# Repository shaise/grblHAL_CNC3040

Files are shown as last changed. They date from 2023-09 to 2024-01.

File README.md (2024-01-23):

# grblHAL_CNC3040 [WIP]
Hardware implementation of the grblHAL driver to work with Chinese CNC3040 type of machines  

This project is intended to upgrade any cnc machine that is controlled via parallel port such as the popular chinese CNC3040.  
Instead of having a dedicated LinuxCNC PC or mach32, This device connects directly to the CNC's controller, and can be controlled using any grbl Sender sw via USB connection or even WiFi!  
This device supports an optional stand-alone KeyPad, that is also included in this project.  

This project is based on the great work of @terjeio and his [GrblHAL](https://github.com/grblHAL) project. Thanks!

## Some images:
Open driver  
Closed driver  
Keypad  

## Driver and KeyPad Assembly:
For instructions how to assemble, program and use the devices refer to the Wiki.

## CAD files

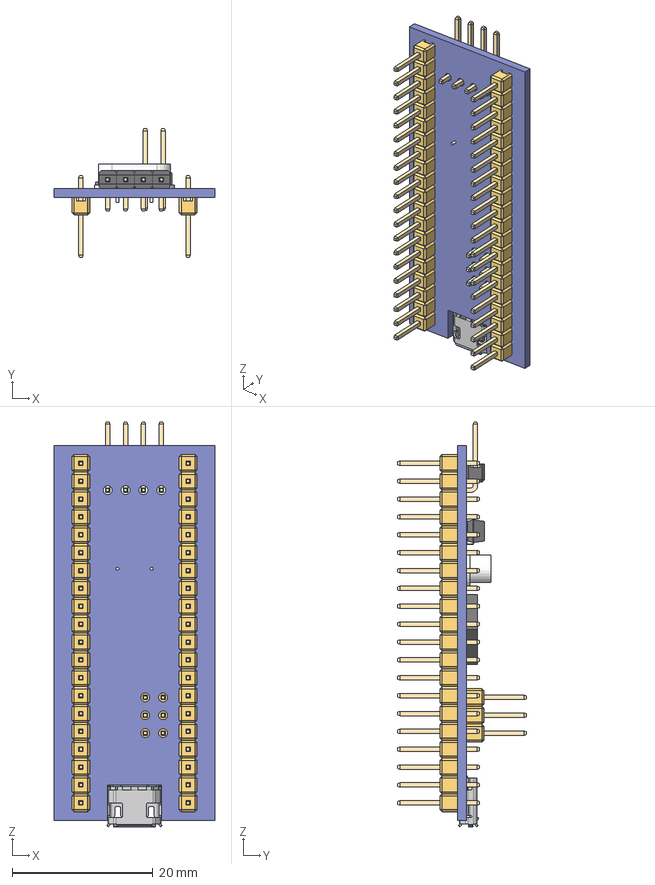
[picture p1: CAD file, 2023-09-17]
hardware/CNC3040_Keypad/models/STM32F103C8T6_Blue_Pill v6.step
22.9 x 18.3 x 57.6 mm
Oscillator_HC-49/S
STM32F103C8T6_BluePill_Board
Oscillator_MC-306
STM32_LQFP48
Tactile_SMD_5x5mm
Header_L4_10x4.8
Header_Male_2x3x11.6
Header_Male_1x20x11.6 x 2

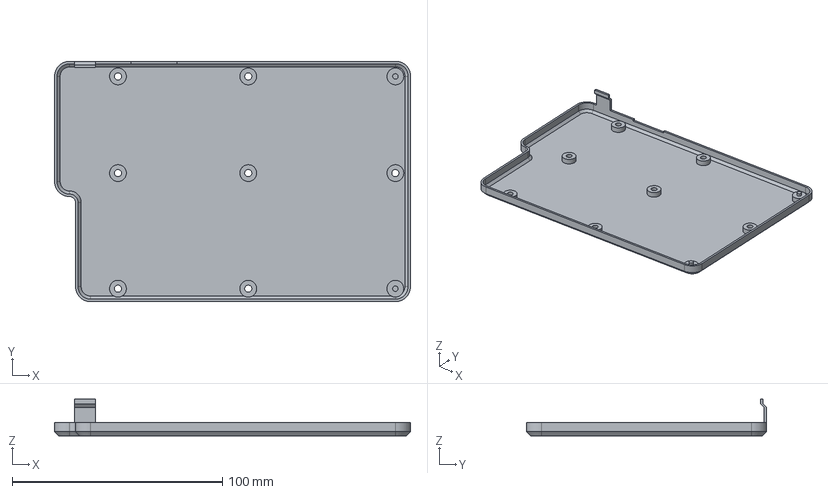
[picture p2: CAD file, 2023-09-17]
mechanics/KeyPadBox.FCStd
169.4 x 114.4 x 17.4 mm

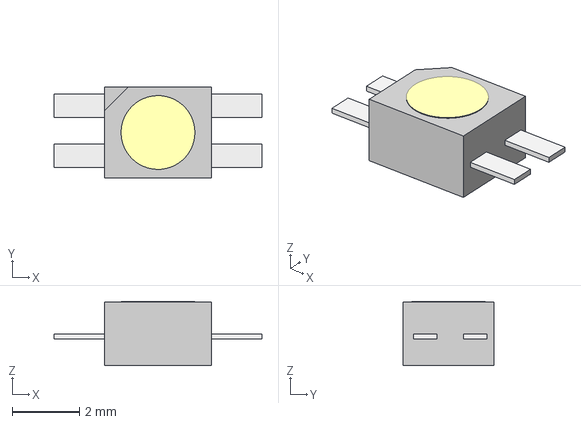
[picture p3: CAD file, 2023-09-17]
hardware/CNC3040_Keypad/models/LTST-A683CEGBW.step
6.20 x 2.70 x 1.92 mm

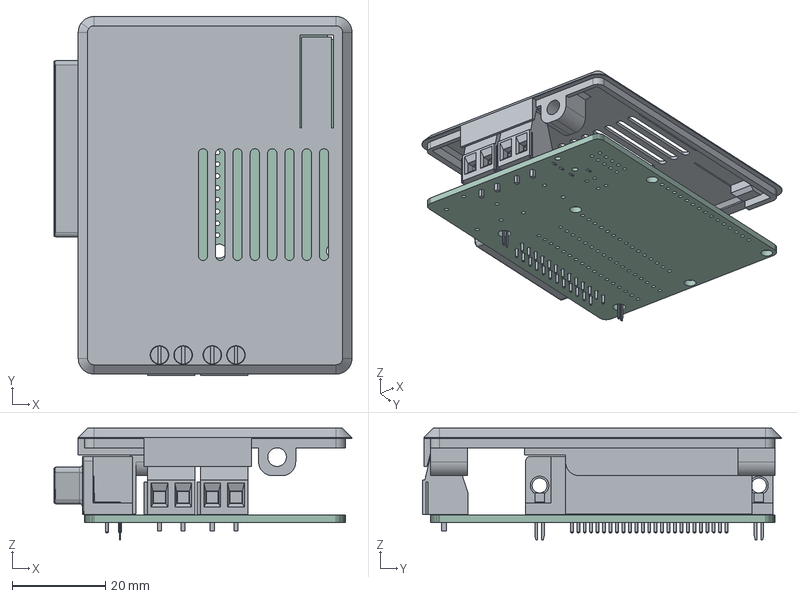
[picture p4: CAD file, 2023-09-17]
mechanics/CNC3040_Box.FCStd
64.0 x 77.1 x 24.0 mm
GrblHAL_CNC3040 PCB
Top

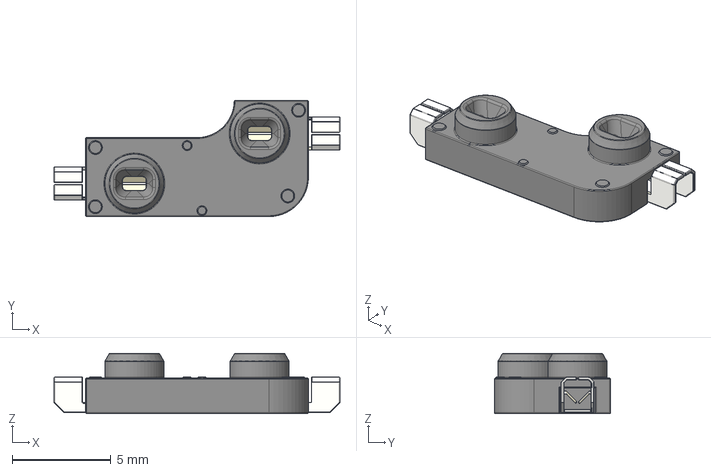
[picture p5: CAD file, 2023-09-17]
hardware/CNC3040_Keypad/models/KailhSocket.stp
14.5 x 5.89 x 3.05 mm

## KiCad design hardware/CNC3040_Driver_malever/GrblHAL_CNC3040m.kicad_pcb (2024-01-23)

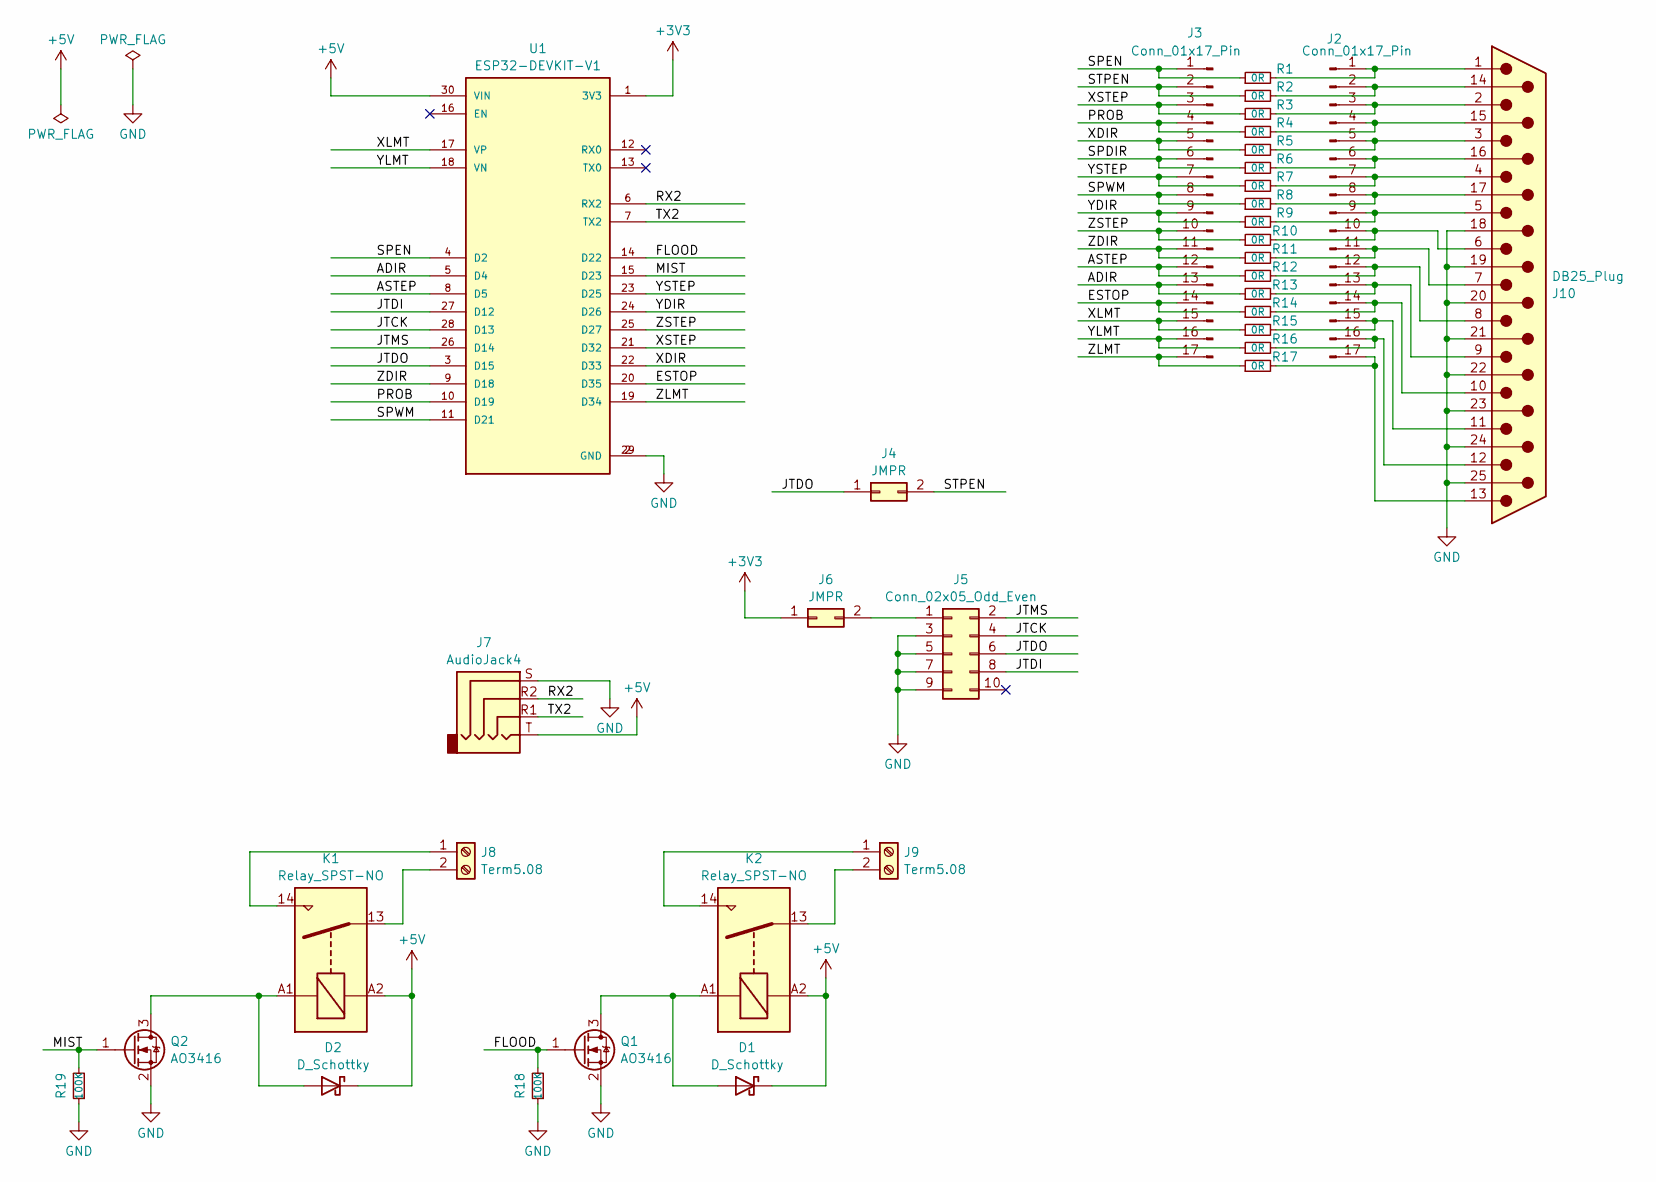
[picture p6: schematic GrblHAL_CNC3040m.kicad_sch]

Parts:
D1, D2: D_Schottky; D_SMA
J2, J3: Conn_01x17_Pin; PinHeader_1x17_P2.54mm_Vertical
J4, J6: JMPR; PinHeader_1x02_P2.54mm_Vertical
J5: Conn_02x05_Odd_Even; IDC-Header_2x05_P2.54mm_Vertical
J7: AudioJack4; Jack_3.5mm_PJ-320A
J8, J9: Term5.08; TerminalBlock_Phoenix_MKDS-1,5-2-5.08_1x02_P5.08mm_Horizont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
J10: DB25_Plug; DSUB-25_Male_Horizontal_P2.77x2.84mm_EdgePinOffset4.94mm_Ho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
K1, K2: Relay_SPST-NO; Relay_HF32FV-G
Q1, Q2: AO3416; SOT-23-3
R1, R2, R3, R4, R5, R6, R7, R8, R9, R10, R11, R12, R13, R14, R15, R16, R17: 0R; R_0603_1608Metric
R18, R19: 100K; R_0603_1608Metric
U1: ESP32-DEVKIT-V1; MODULE_ESP32_DEVKIT_V1; PARTREV N/A

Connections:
+3V3: J6.1, U1.1 (3V3)
+5V: D1.1 (K), D2.1 (K), J7.T, K1.A2, K2.A2, U1.30 (VIN)
/ADIR: J3.13, R13.1, U1.5 (D4)
/ASTEP: J3.12, R12.1, U1.8 (D5)
/ESTOP: J3.14, R14.1, U1.20 (D35)
/FLOOD: Q1.1 (G), R18.2, U1.14 (D22)
/JTCK: J5.4, U1.28 (D13)
/JTDI: J5.8, U1.27 (D12)
/JTDO: J4.1, J5.6, U1.3 (D15)
/JTMS: J5.2, U1.26 (D14)
/MIST: Q2.1 (G), R19.2, U1.15 (D23)
/PROB: J3.4, R4.1, U1.10 (D19)
/RX2: J7.R2, U1.6 (RX2)
/SPDIR: J3.6, R6.1
/SPEN: J3.1, R1.1, U1.4 (D2)
/SPWM: J3.8, R8.1, U1.11 (D21)
/STPEN: J3.2, J4.2, R2.1
/TX2: J7.R1, U1.7 (TX2)
/XDIR: J3.5, R5.1, U1.22 (D33)
/XLMT: J3.15, R15.1, U1.17 (VP)
/XSTEP: J3.3, R3.1, U1.21 (D32)
/YDIR: J3.9, R9.1, U1.24 (D26)
/YLMT: J3.16, R16.1, U1.18 (VN)
/YSTEP: J3.7, R7.1, U1.23 (D25)
/ZDIR: J3.11, R11.1, U1.9 (D18)
/ZLMT: J3.17, R17.1, U1.19 (D34)
/ZSTEP: J3.10, R10.1, U1.25 (D27)
GND: J5.3, J5.5, J5.7, J5.9, J7.S, J10.18, J10.19, J10.20, J10.21, J10.22, J10.23, J10.24, J10.25, Q1.2 (S), Q2.2 (S), R18.1, R19.1, U1.2 (GND), U1.29 (GND)
unnamed: D1.2 (A), K2.A1, Q1.3 (D)
unnamed: D2.2 (A), K1.A1, Q2.3 (D)
unnamed: J2.1, J10.1, R1.2
unnamed: J2.3, J10.2, R3.2
unnamed: J2.5, J10.3, R5.2
unnamed: J2.7, J10.4, R7.2
unnamed: J2.9, J10.5, R9.2
unnamed: J2.10, J10.6, R10.2
unnamed: J2.11, J10.7, R11.2
unnamed: J2.12, J10.8, R12.2
unnamed: J2.13, J10.9, R13.2
unnamed: J2.14, J10.10, R14.2
unnamed: J2.15, J10.11, R15.2
unnamed: J2.16, J10.12, R16.2
unnamed: J2.17, J10.13, R17.2
unnamed: J5.1, J6.2
unnamed: J8.1, K1.14
unnamed: J8.2, K1.13
unnamed: J9.1, K2.14
unnamed: J9.2, K2.13
unnamed: J2.2, J10.14, R2.2
unnamed: J2.4, J10.15, R4.2
unnamed: J2.6, J10.16, R6.2
unnamed: J2.8, J10.17, R8.2

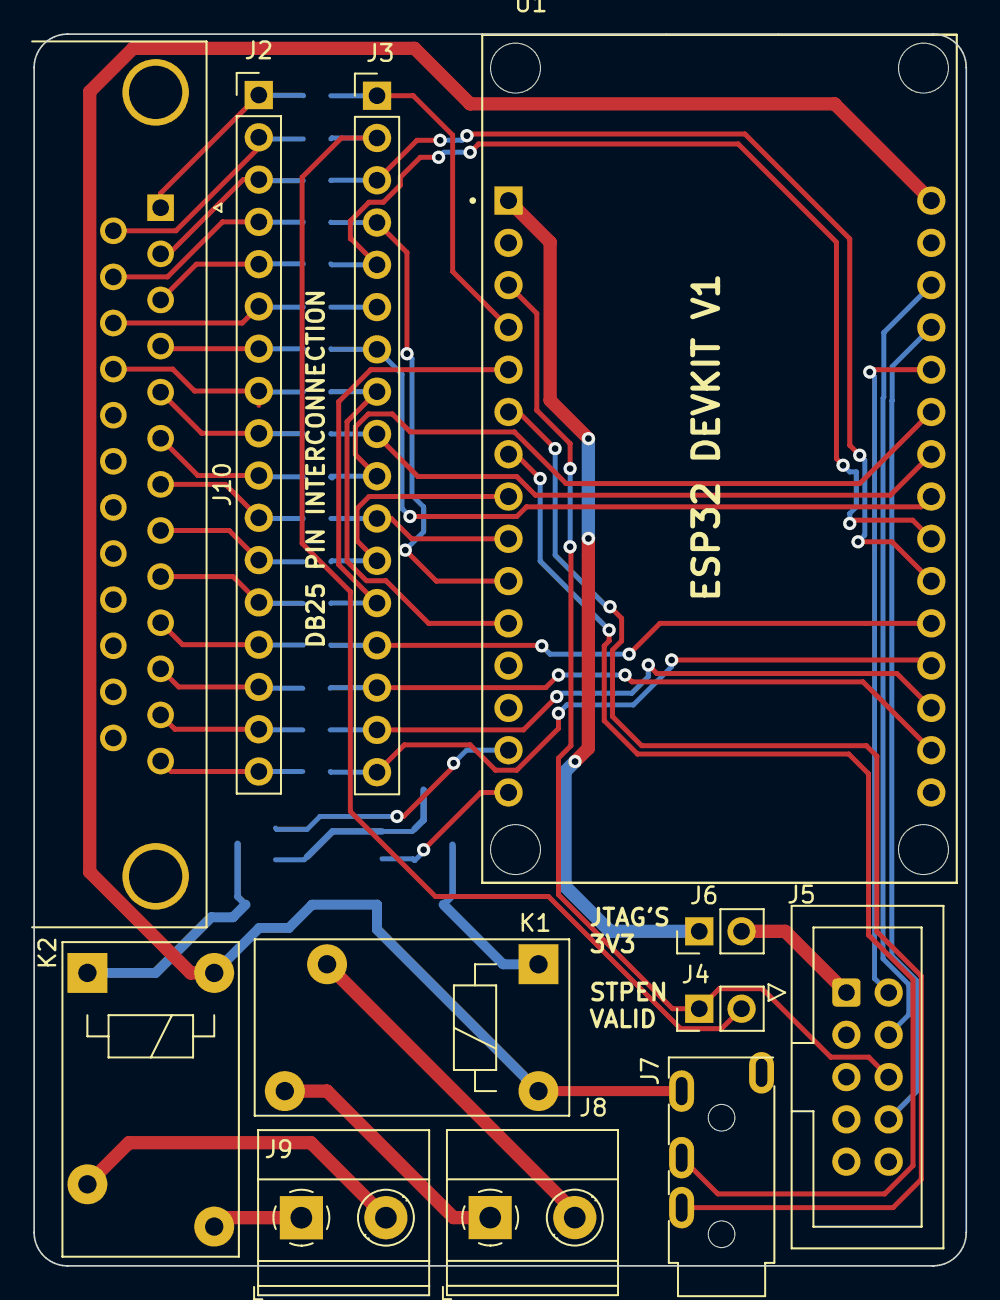
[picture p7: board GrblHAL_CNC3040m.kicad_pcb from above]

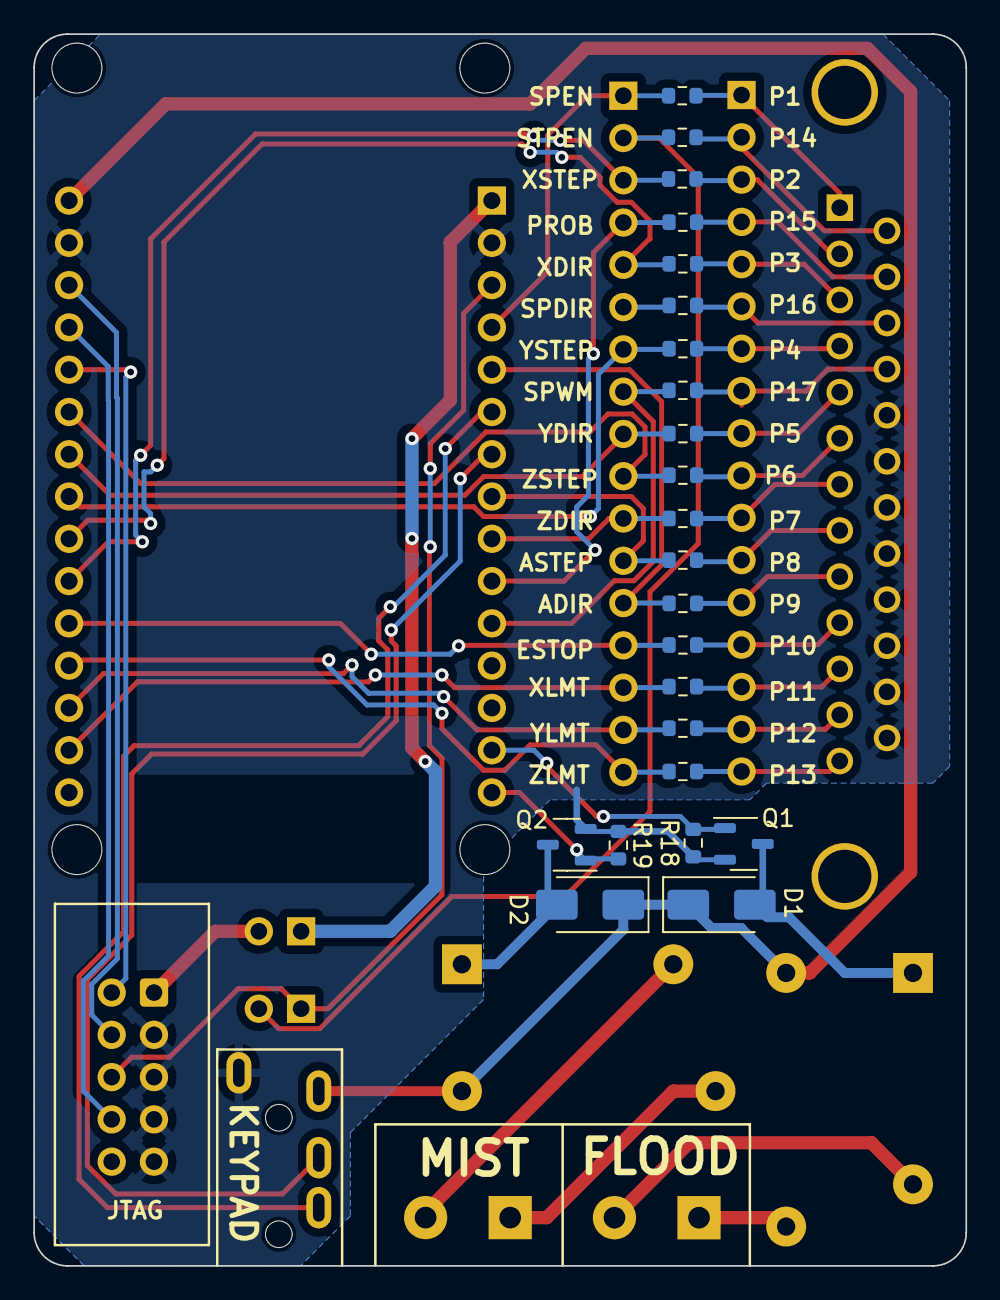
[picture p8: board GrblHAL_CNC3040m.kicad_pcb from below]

Board: 2 copper layers, 56.0 x 74.0 mm, 35 parts (23 on the bottom side), 52 nets.

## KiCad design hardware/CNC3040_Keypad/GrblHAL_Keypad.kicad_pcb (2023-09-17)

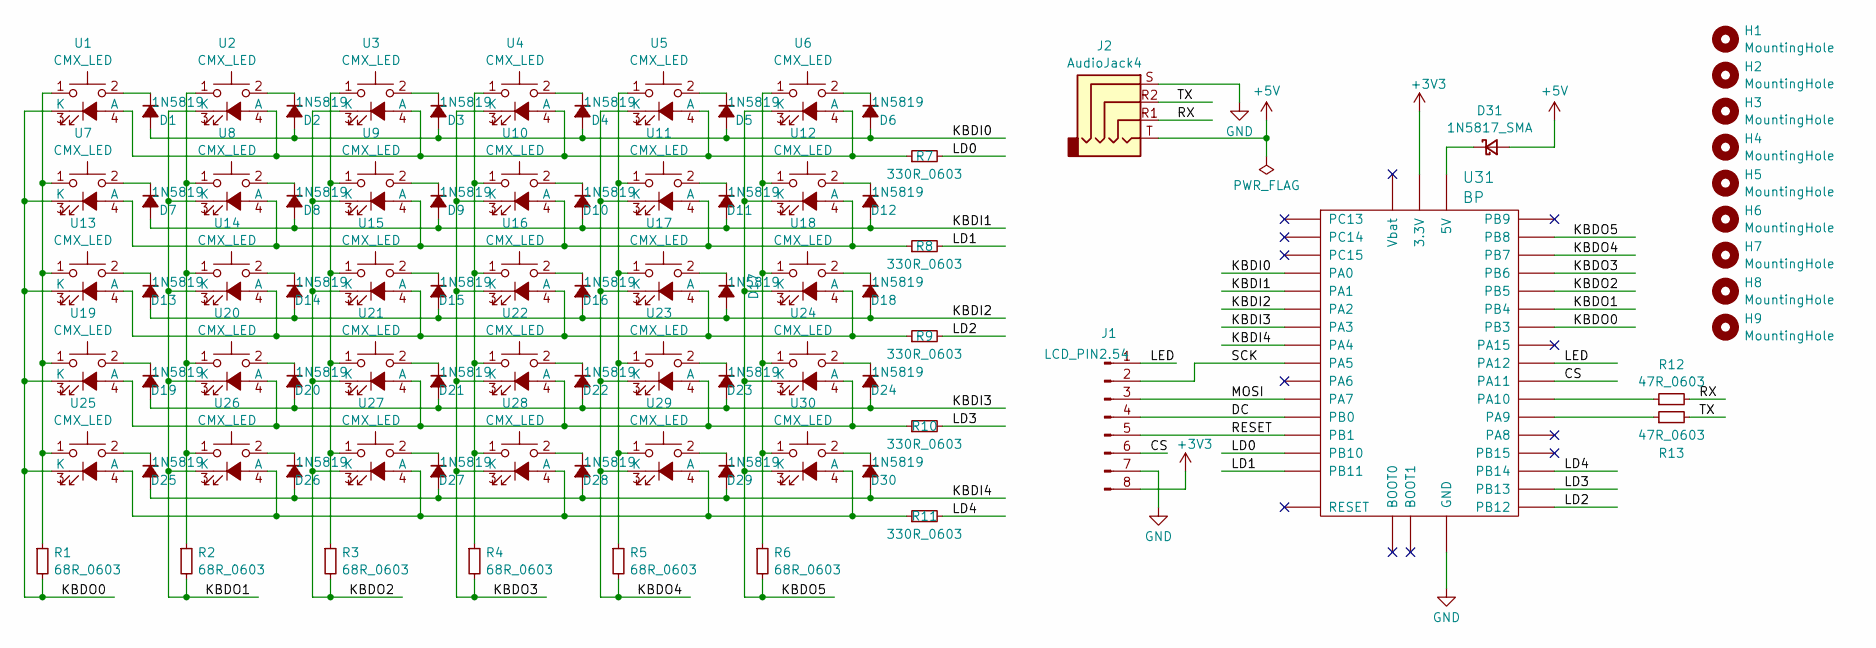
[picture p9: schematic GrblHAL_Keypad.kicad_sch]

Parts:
D1, D2, D3, D4, D5, D6, D7, D8, D9, D10, D11, D12, D13, D14, D15, D16, D17, D18, D19, D20, D21, D22, D23, D24, D25, D26, D27, D28, D29, D30: 1N5819; D_SOD-123
D31: 1N5817_SMA; D_SMA
H1, H2, H3, H4, H5, H6, H7, H8, H9: MountingHole; MountingHole_3.2mm_M3
J1: LCD_PIN2.54; PinHeader_1x08_P2.54mm_Vertical
J2: AudioJack4; Jack_3.5mm_PJ-320A
R1, R2, R3, R4, R5, R6: 68R_0603; R_0603_1608Metric
R7, R8, R9, R10, R11: 330R_0603; R_0603_1608Metric
R12, R13: 47R_0603; R_0603_1608Metric
U1, U2, U3, U4, U5, U6, U7, U8, U9, U10, U11, U12, U13, U14, U15, U16, U17, U18, U19, U20, U21, U22, U23, U24, U25, U26, U27, U28, U29, U30: CMX_LED; CherryMX_1.00u_KailhSocket_LED
U31: BP; BLUEPILL-BARE

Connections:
+3V3: J1.8, U31.3V3 (3.3V)
+5V: D31.2 (A), J2.T
/CS: J1.6, U31.PA11
/DC: J1.4, U31.PB0
/KBDI0: D1.2 (A), D2.2 (A), D3.2 (A), D4.2 (A), D5.2 (A), D6.2 (A), U31.PA0
/KBDI1: D7.2 (A), D8.2 (A), D9.2 (A), D10.2 (A), D11.2 (A), D12.2 (A), U31.PA1
/KBDI2: D13.2 (A), D14.2 (A), D15.2 (A), D16.2 (A), D17.2 (A), D18.2 (A), U31.PA2
/KBDI3: D19.2 (A), D20.2 (A), D21.2 (A), D22.2 (A), D23.2 (A), D24.2 (A), U31.PA3
/KBDI4: D25.2 (A), D26.2 (A), D27.2 (A), D28.2 (A), D29.2 (A), D30.2 (A), U31.PA4
/KBDO0: R1.2, U1.3 (K), U7.3 (K), U13.3 (K), U19.3 (K), U25.3 (K), U31.PB3
/KBDO1: R2.2, U2.3 (K), U8.3 (K), U14.3 (K), U20.3 (K), U26.3 (K), U31.PB4
/KBDO2: R3.2, U3.3 (K), U9.3 (K), U15.3 (K), U21.3 (K), U27.3 (K), U31.PB5
/KBDO3: R4.2, U4.3 (K), U10.3 (K), U16.3 (K), U22.3 (K), U28.3 (K), U31.PB6
/KBDO4: R5.2, U5.3 (K), U11.3 (K), U17.3 (K), U23.3 (K), U29.3 (K), U31.PB7
/KBDO5: R6.2, U6.3 (K), U12.3 (K), U18.3 (K), U24.3 (K), U30.3 (K), U31.PB8
/LD0: R7.2, U31.PB10
/LD1: R8.2, U31.PB11
/LD2: R9.2, U31.PB12
/LD3: R10.2, U31.PB13
/LD4: R11.2, U31.PB14
/LED: J1.1, U31.PA12
/MOSI: J1.3, U31.PA7
/RESET: J1.5, U31.PB1
/RX: J2.R1, R12.2
/SCK: J1.2, U31.PA5
/TX: J2.R2, R13.2
GND: J1.7, J2.S, U31.G (GND)
unnamed: D1.1 (K), U1.2
unnamed: D2.1 (K), U2.2
unnamed: D3.1 (K), U3.2
unnamed: D4.1 (K), U4.2
unnamed: D5.1 (K), U5.2
unnamed: D6.1 (K), U6.2
unnamed: D7.1 (K), U7.2
unnamed: D8.1 (K), U8.2
unnamed: D9.1 (K), U9.2
unnamed: D10.1 (K), U10.2
unnamed: D11.1 (K), U11.2
unnamed: D12.1 (K), U12.2
unnamed: D13.1 (K), U13.2
unnamed: D14.1 (K), U14.2
unnamed: D15.1 (K), U15.2
unnamed: D16.1 (K), U16.2
unnamed: D17.1 (K), U17.2
unnamed: D18.1 (K), U18.2
unnamed: D19.1 (K), U19.2
unnamed: D20.1 (K), U20.2
unnamed: D21.1 (K), U21.2
unnamed: D22.1 (K), U22.2
unnamed: D23.1 (K), U23.2
unnamed: D24.1 (K), U24.2
unnamed: D25.1 (K), U25.2
unnamed: D26.1 (K), U26.2
unnamed: D27.1 (K), U27.2
unnamed: D28.1 (K), U28.2
unnamed: D29.1 (K), U29.2
unnamed: D30.1 (K), U30.2
unnamed: D31.1 (K), U31.5V
unnamed: R1.1, U1.1, U7.1, U13.1, U19.1, U25.1
unnamed: R2.1, U2.1, U8.1, U14.1, U20.1, U26.1
unnamed: R3.1, U3.1, U9.1, U15.1, U21.1, U27.1
unnamed: R4.1, U4.1, U10.1, U16.1, U22.1, U28.1
unnamed: R5.1, U5.1, U11.1, U17.1, U23.1, U29.1
unnamed: R6.1, U6.1, U12.1, U18.1, U24.1, U30.1
unnamed: R12.1, U31.PA10
unnamed: R13.1, U31.PA9
unnamed: R7.1, U1.4 (A), U2.4 (A), U3.4 (A), U4.4 (A), U5.4 (A), U6.4 (A)
unnamed: R8.1, U7.4 (A), U8.4 (A), U9.4 (A), U10.4 (A), U11.4 (A), U12.4 (A)
unnamed: R9.1, U13.4 (A), U14.4 (A), U15.4 (A), U16.4 (A), U17.4 (A), U18.4 (A)
unnamed: R10.1, U19.4 (A), U20.4 (A), U21.4 (A), U22.4 (A), U23.4 (A), U24.4 (A)
unnamed: R11.1, U25.4 (A), U26.4 (A), U27.4 (A), U28.4 (A), U29.4 (A), U30.4 (A)

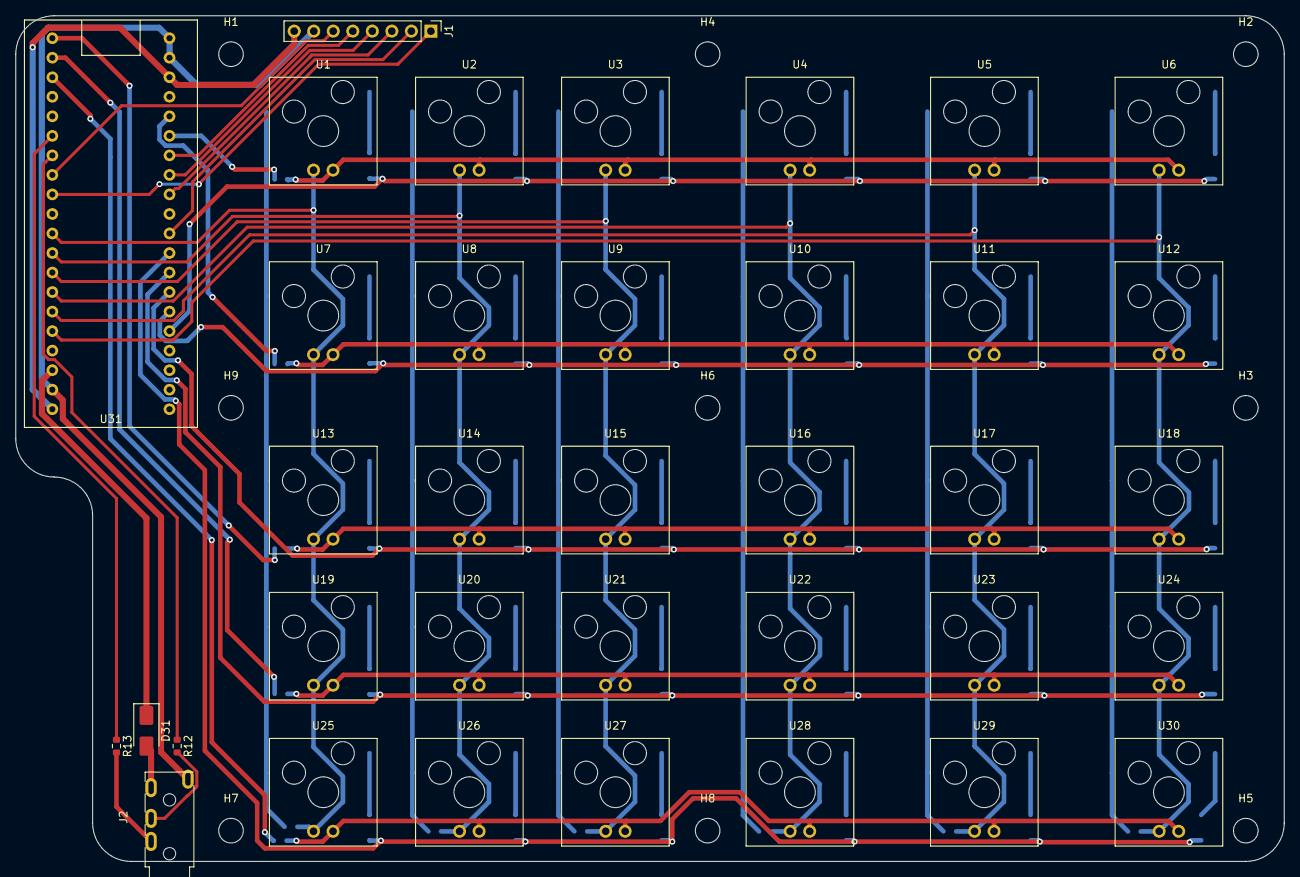
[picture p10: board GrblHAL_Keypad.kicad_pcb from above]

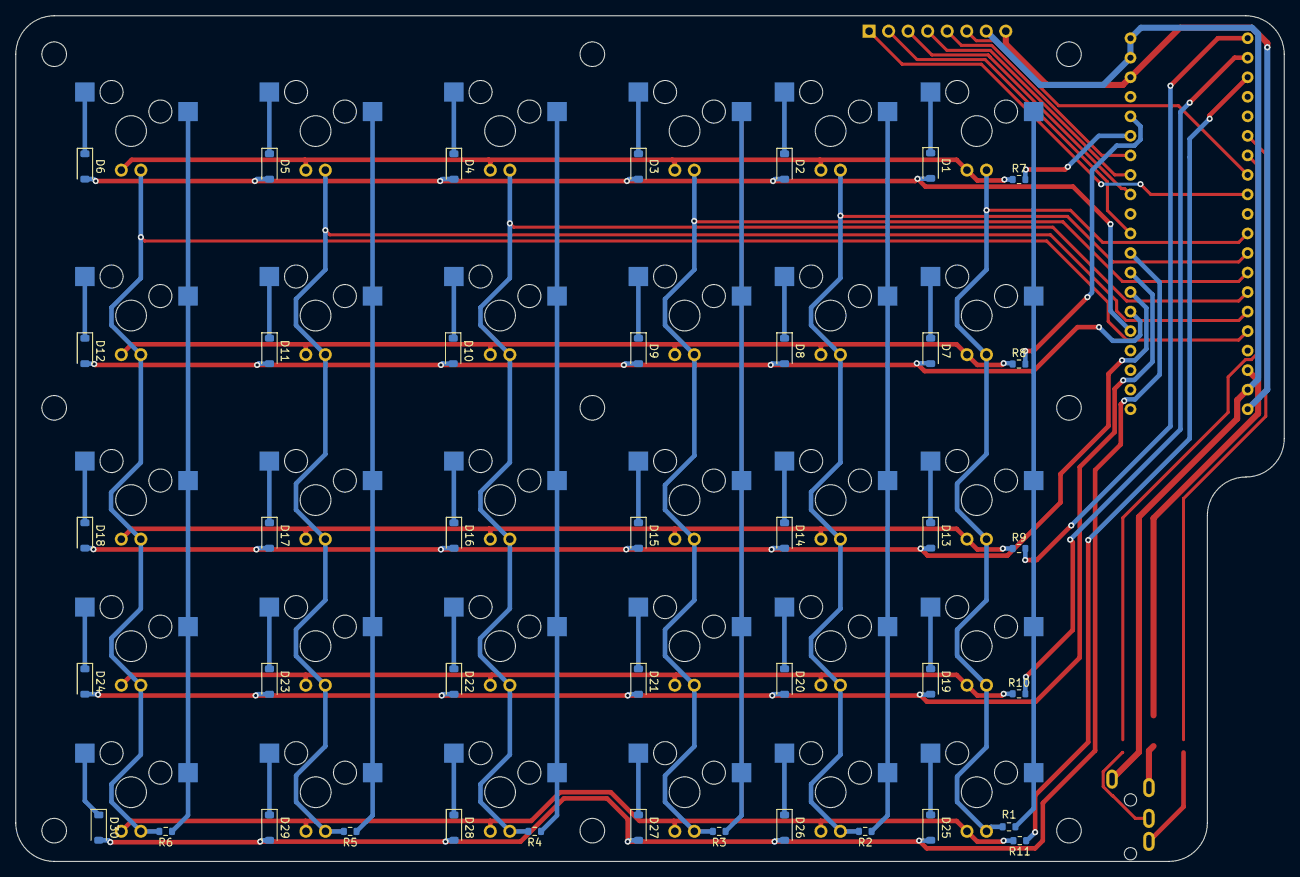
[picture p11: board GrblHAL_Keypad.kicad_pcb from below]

Board: 2 copper layers, 165.0 x 110.0 mm, 86 parts (41 on the bottom side), 71 nets.

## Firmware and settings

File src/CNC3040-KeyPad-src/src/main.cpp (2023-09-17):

#include <Arduino.h>
#include "key_defs.h"

const uint8_t input_ios[] = {PA0, PA1, PA2, PA3, PA4};
const uint8_t output_ios[] = {PB3, PB4, PB5, PB6, PB7, PB8, PB10, PB11, PB12, PB13, PB14};
#define NUM_INPUTS sizeof(input_ios)
#define NUM_OUTPUTS sizeof(output_ios)

// scan from PB3 to PB8 
#define SCAN_START (1<<3)
#define SCAN_END   (1<<8)
#define SCAN_OUT_MASK 0x1F8
#define SCAN_IN_MASK 0x1F
#define SCAN_LED_MASK 0x7C00
int line_shift = SCAN_START; 
int line_count = 0;

uint32_t last_but_state, cur_but_state = 0;
uint32_t led_state = 0;
uint32_t last_millis = 0, cur_millis;

void setup() {
  Serial.begin(115200);
  Serial1.begin(115200);
  for (int i = 0; i < NUM_INPUTS; i++)
    pinMode(input_ios[i], INPUT_PULLUP);
  for (int i = 0; i < NUM_OUTPUTS; i++)
    pinMode(output_ios[i], OUTPUT);
  //GPIOB->ODR = SCAN_LED_MASK;
}

uint32_t presslap;

void SendCmd(uint8_t cmd)
{
  Serial1.write(cmd);
  //Serial.println(cmd, 16);
}

void HandleDirectMap(const uint32_t *map, int press_mask)
{
  while (*map != 0)
  {
    uint32_t key = *map++;
    uint8_t cmd = (uint8_t)*map++;
    if (press_mask & key)
      SendCmd(cmd);
  }
}

void HandleKeyPressed(int press_mask)
{
  #define IF_PRESSED(x) if (press_mask & (x))
  if (press_mask == 0)
    return;
  presslap = millis();
  HandleDirectMap(jog_key_map, press_mask);
  HandleDirectMap(motion_key_map, press_mask);
  HandleDirectMap(control_key_map, press_mask);

}

void HandleKeyReleased(int release_mask)
{
  #define IF_RELEASED(x) if (press_mask & (x))
  if (release_mask == 0)
    return;
  
  //Serial.println(millis()-presslap);
  // any key release will cancel jog motion
  SendCmd(CMD_CANCL_JOG);
}


void poll_buttons_leds()
{
  int in, leds, shift;
  in = (int)GPIOA->IDR & SCAN_IN_MASK;
  shift = line_count * 5;
  cur_but_state &= ~(SCAN_IN_MASK << shift);
  cur_but_state |= (in ^ SCAN_IN_MASK) << shift;
  line_shift <<= 1;
  line_count++;
  if (line_count >= 6)
  {
    line_shift = SCAN_START;
    line_count = 0;
  }
  GPIOB->BRR = SCAN_LED_MASK;
  shift = line_count * 5;
  leds = (led_state >> shift) & 0x1F;
  GPIOB->BSRR = SCAN_OUT_MASK | leds << 10;
  //GPIOB->BSRR = leds << 10;
  GPIOB->BRR = line_shift;

  // look for key press/release
  if (cur_but_state != last_but_state)
  {
    //Serial.println((int)GPIOB->ODR & SCAN_LED_MASK, 16);
    //Serial.println(cur_but_state, 16);
    uint32_t changes = last_but_state ^ cur_but_state;
    HandleKeyPressed(changes & cur_but_state);
    HandleKeyReleased(changes & ~cur_but_state);
    last_but_state = cur_but_state;
    led_state = cur_but_state;
    //Serial1.write((uint8_t)0xA5);
  }

}



void loop() {
  cur_millis = millis();
  if (cur_millis == last_millis)
    return; 
  
  poll_buttons_leds();
  last_millis = cur_millis;

  if (Serial1.available())
  {
    Serial.print("Got: ");
    Serial.println((int)Serial1.read(), 16);
  }
}

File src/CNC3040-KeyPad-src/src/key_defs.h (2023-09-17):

#ifndef __KEY_DEFS_H__
#define __KEY_DEFS_H__

#define KEY_CYCLE_START  0x00000001
#define KEY_SPIN_M10     0x00000002
#define KEY_AM           0x00000004
#define KEY_XM           0x00000008
#define KEY_BM           0x00000010
#define KEY_FEED_HOLD    0x00000020
#define KEY_SPIN_ON_OFF  0x00000040
#define KEY_YP           0x00000080
#define KEY_JOG_MODE     0x00000100
#define KEY_YM           0x00000200
#define KEY_AUX1         0x00000400
#define KEY_SPIN_P10     0x00000800
#define KEY_AP           0x00001000
#define KEY_XP           0x00002000
#define KEY_BP           0x00004000
#define KEY_ALARM_OFF    0x00008000
#define KEY_HOME         0x00010000
#define KEY_ZP           0x00020000
#define KEY_AUX2         0x00040000
#define KEY_ZM           0x00080000
#define KEY_DOOR         0x00100000
#define KEY_MIST         0x00200000
#define KEY_FEED_P10     0x00400000
#define KEY_FEED_100     0x00800000
#define KEY_FEED_M10     0x01000000
#define KEY_ESTOP        0x02000000
#define KEY_FLOOD        0x04000000
#define KEY_RAPID_100    0x08000000
#define KEY_RAPID_50     0x10000000
#define KEY_RAPID_25     0x20000000


#define CMD_FEED_HOLD '!'  // 	Enter feed hold
#define CMD_CYC_START '~'  // 	Cycle start
#define CMD_EN_MPG    0x8B //   Enable MPG full control1
#define CMD_CANCL_JOG 0x85 //   Cancel jog motion2
#define CMD_STEP_JOG  '0'  // 	Enable step mode jogging
#define CMD_SLOW_JOG  '1'  // 	Enable slow jogging mode
#define CMD_FAST_JOG  '2'  // 	Enable fast jogging mode
#define CMD_NEXT_JOG  'h'  // 	Select next jog mode
#define CMD_HOME      'H'  // 	Home machine
#define CMD_JOG_XR    'R'  // 	Continuous jog X+
#define CMD_JOG_XL    'L'  // 	Continuous jog X-
#define CMD_JOG_YF    'F'  // 	Continuous jog Y+
#define CMD_JOG_YB    'B'  // 	Continuous jog Y-
#define CMD_JOG_ZU    'U'  // 	Continuous jog Z+
#define CMD_JOG_ZD    'D'  // 	Continuous jog Z-
#define CMD_JOG_XRYF  'r'  // 	Continuous jog X+Y+
#define CMD_JOG_XRYB  'q'  // 	Continuous jog X+Y-
#define CMD_JOG_XLYF  's'  // 	Continuous jog X-Y+
#define CMD_JOG_XLYB  't'  // 	Continuous jog X-Y-
#define CMD_JOG_XRZU  'w'  // 	Continuous jog X+Z+
#define CMD_JOG_XRZD  'v'  // 	Continuous jog X+Z-
#define CMD_JOG_XLZU  'u'  // 	Continuous jog X-Z+
#define CMD_JOG_XLZD  'x'  // 	Continuous jog X-Z-
#define CMD_JOG_AR    'A'  //    Continuous jog A CW
#define CMD_JOG_AL    'a'  //    Continuous jog A CCW
#define CMD_TOGL_DOOR    0x84 	// Toggle safety door open status
#define CMD_TOGL_OP_STOP 0x88 	// Toggle optional stop mode
#define CMD_TOGL_BLK_EXE 0x89 	// Toggle single block execution mode
#define CMD_TOGL_FAN     0x8A 	// Toggle Fan 0 output3
#define CMD_FEED_100     'I'	// Restore feed override value to 100%
#define CMD_FEED_100X    0x90 	// Restore feed override value to 100%
#define CMD_FEED_P10     'i' 	// Increase feed override value 10%
#define CMD_FEED_P10X    0x91 	// Increase feed override value 10%
#define CMD_FEED_M10     'j' 	// Decrease feed override value 10%
#define CMD_FEED_M10X    0x92 	// Decrease feed override value 10%
#define CMD_FEED_P1      0x93 	// Increase feed override value 1%
#define CMD_FEED_M1      0x94 	// Decrease feed override value 1%
#define CMD_RAPID_100    0x95 	// Restore rapids override value to 100%
#define CMD_RAPID_50     0x96 	// Set rapids override to 50%
#define CMD_RAPID_25     0x97 	// Set rapids override to 25%
#define CMD_SPIN_100     'K' 	// Restore spindle RPM override value to 100%
#define CMD_SPIN_100X    0x99 	// Restore spindle RPM override value to 100%
#define CMD_SPIN_P10     'k' 	// Increase spindle RPM override value 10%
#define CMD_SPIN_P10X    0x9A 	// Increase spindle RPM override value 10%
#define CMD_SPIN_M10     'z' 	// Decrease spindle RPM override value 10%
#define CMD_SPIN_M10X    0x9B 	// Decrease spindle RPM override value 10%
#define CMD_SPIN_P1      0x9C 	// Increase spindle RPM override value 1%
#define CMD_SPIN_M1      0x9D 	// Decrease spindle RPM override value 1%
#define CMD_SPIN_STOP    0x9E 	// Toggle spindle stop override4
#define CMD_TOGL_FLOOD   'C' 	// Toggle flood coolant output
#define CMD_TOGL_FLOODX  0xA0 	// Toggle flood coolant output
#define CMD_TOGL_MIST    'M' 	// Toggle mist coolant output
#define CMD_TOGL_MISTX   0xA1 	// Toggle mist coolant output

extern const uint32_t jog_key_map[];
extern const uint32_t motion_key_map[];
extern const uint32_t control_key_map[];






#endif

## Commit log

2023-09-19 add bom
2024-01-23 add male version of the driver
    [GrblHAL_CNC3040m.kicad_pcb, GrblHAL_CNC3040m.kicad_sch]
